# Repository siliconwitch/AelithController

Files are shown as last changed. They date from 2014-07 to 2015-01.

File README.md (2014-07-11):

# Project Aelith Digital Controller
=================================

An embedded control system targeted to RC model cars which feature individual wheel drive. This controller allows for software differentials and power delivery with the aid of various sensors on the vehicle. Currently the system makes use of wheel speed sensors and a 6 axis IMU for real time processing.

Overview Video: http://youtu.be/ET1HEyqEQJQ

The controller communicates to a steering servo and four brushless DC motor controllers. It also listens to a standard RC radio receiver for user input, as well as a serial port for telemetry over wireless modules such as xbee or bluetooth.

It's hoped that this project allows for advanced features such as traction control, under/over steer detection, adaptive power delivery and real-time telemetry.

The system runs on Cortex M4 STM32F4 devices by ST microelectronics. To build this project, you will need the ARM-GCC compiler found here:

https://launchpad.net/gcc-arm-embedded

As well as the STLink driver for uploading to a development board such as the STM32F4Discovery board:

http://www.st.com/web/en/catalog/tools/FM146/CL1984/SC724/SS1677/PF251168

To enable debugging, GDB is required and can be found here:

http://www.emb4fun.de/archive/stlink/index.html

The make.bat file is able to run under Windows to compile, upload and start the debug server. Please ensure that your PATH environment variable are set up in windows for the batch commands to be recognized.

Control System
--------------
The control system for the project is designed in Simulink and can be exported as C code using the embedded coder module. Granted this is the only part of the project that requires a non free software, the exported code however is still in readable C. Useful resource: http://www.mathworks.co.uk/hardware-support/arm-cortex-m-cmsis.html and http://www.mathworks.co.uk/hardware-support/st-discovery-board.html

PCB Info
--------

The hardware used in the project is custom. To see the Schematic, Gerber and Diptrace project files, please see the PCB folder.
Bare boards are available to order at: https://oshpark.com/shared_projects/t9Uw3F4U

CAD Designs
-----------

I'll upload full documentation soon on how to modify a Schumacher Mi5 chassis to support four motors, in the meantime, the CAD files for motor mounts, couplings and suspension mounts can be found in the mechanical folder

Copyright
---------

Copyright (C) 2014 Rajesh Nakarja. All rights reserved
http://www.naklojik.com

This is free software; you can redistribute it and/or modify it under the 
terms of the GNU Lesser General Public License version 3.0.
http://opensource.org/licenses/lgpl-3.0.html

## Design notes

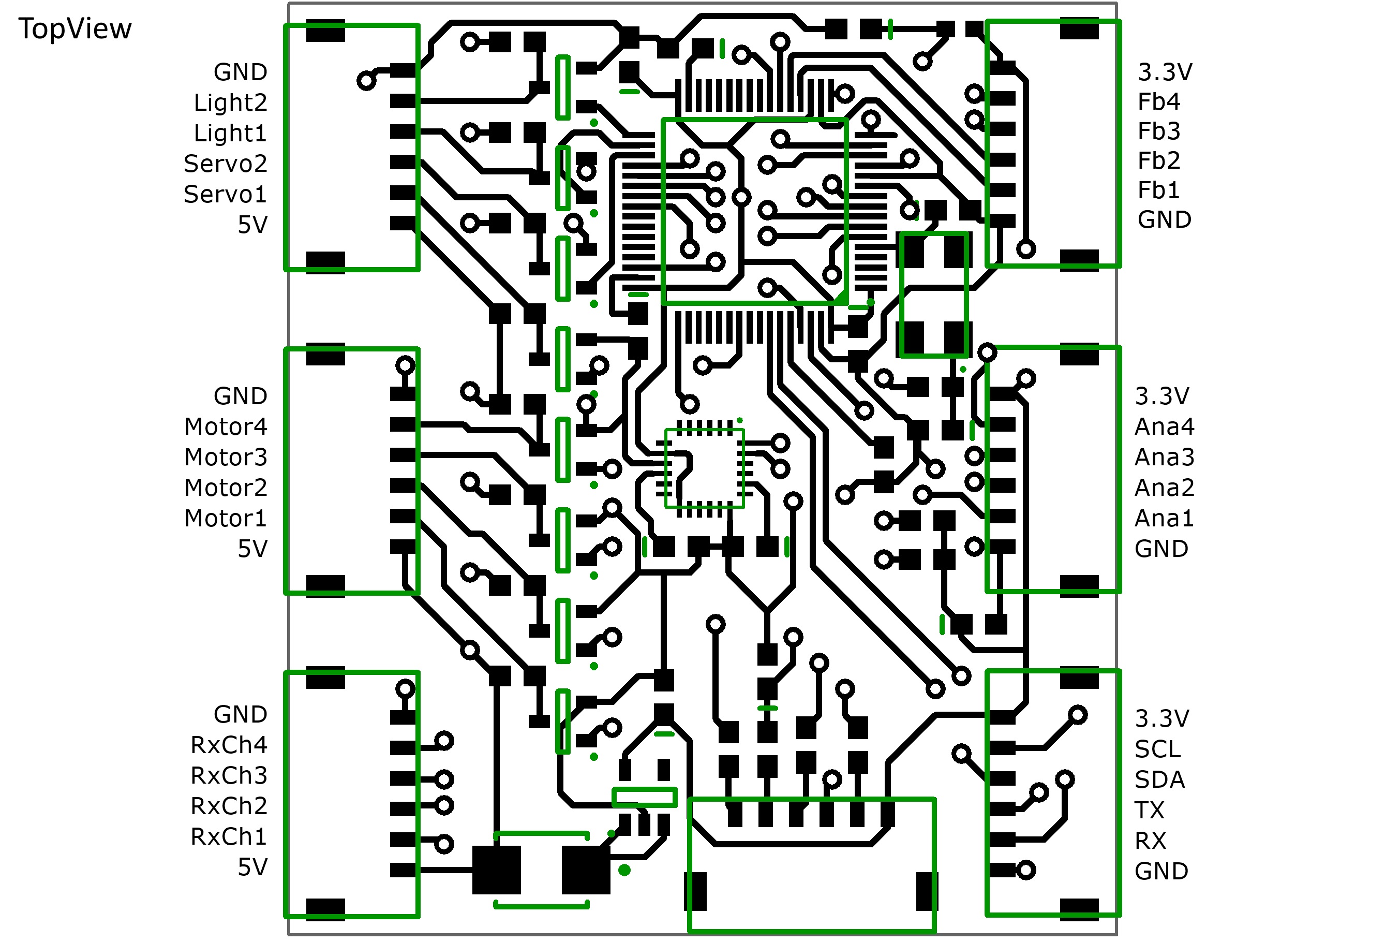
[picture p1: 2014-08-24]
PCB & CAD/PCB Pinout.jpg

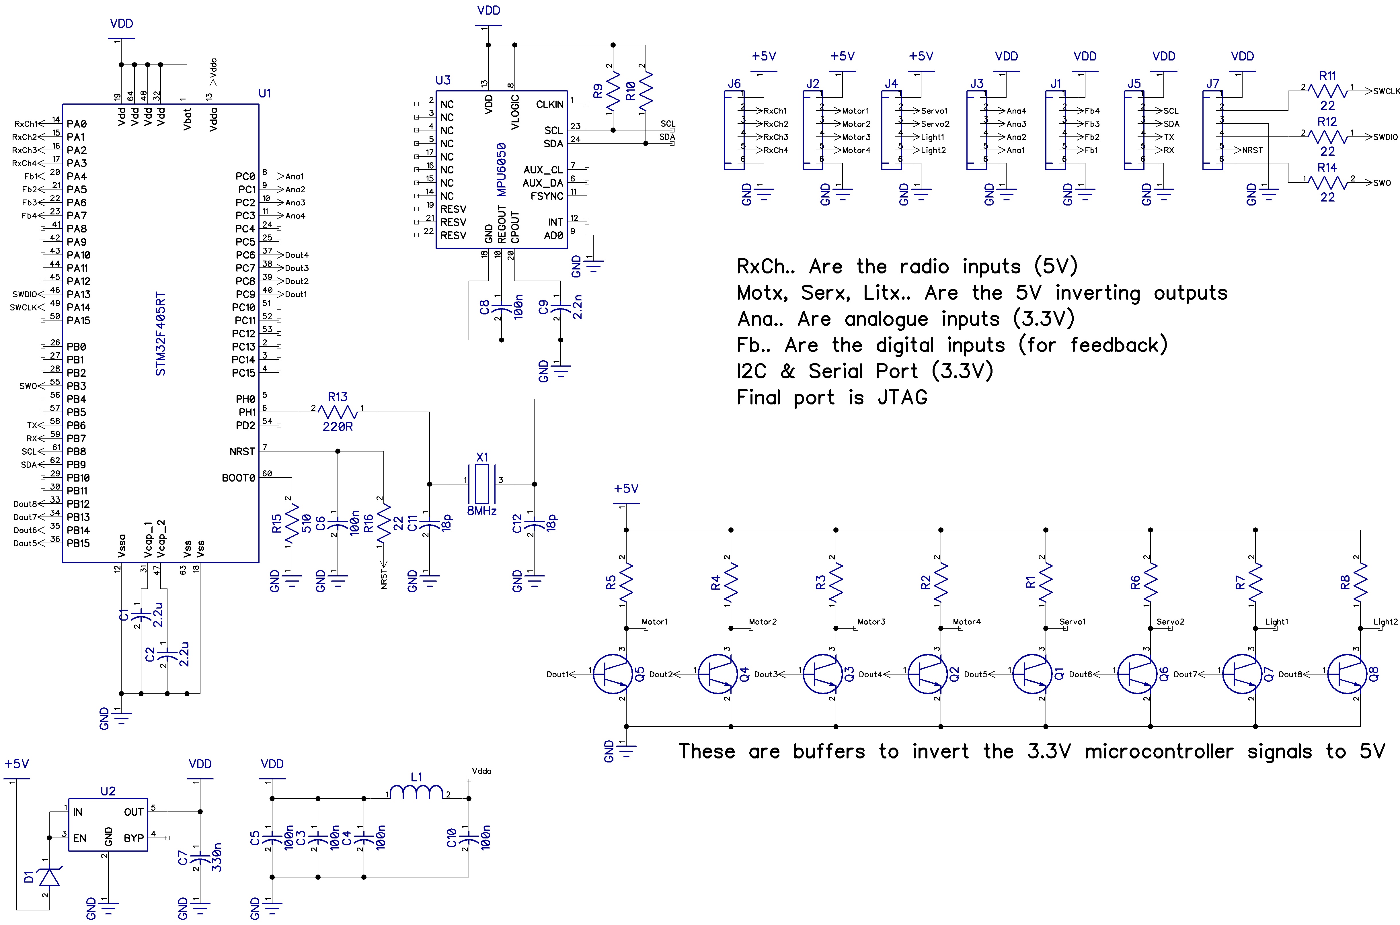
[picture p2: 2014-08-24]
PCB & CAD/Schematic.jpg

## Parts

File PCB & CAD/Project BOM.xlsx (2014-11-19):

Item | Quantity | Single Cost | Total Cost | Link | | | Comments
------------------------------------------------------------------------------------------------------------------------------------------------- |  |  |  |  | | | ---------------------------------------
Schumacher Mi5 | 1 | £344.84 | £344.84 | http://www.wheelspinmodels.co.uk/i/194938/
35A Hobbyking Sensor/Sensorless ESC | 4 | £15.53 | £62.12 | http://www.hobbyking.com/hobbyking/store/__17228__Hobby_King_35A_Sensored_Sensorless_Car_ESC_1_10_1_12_.html
Quadcopter Motors | 4 | £15.89 | £63.56 | http://www.hobbyking.com/hobbyking/store/uh_viewitem.asp?idproduct=41483
Tunigy 4.2 2S2P Shorty Hard Lipo | 1 | £22.14 | £22.14 | http://www.hobbyking.com/hobbyking/store/__23134__Turnigy_nano_tech_Shorty_4200mah_2S2P_65_130C_Hardcase_Lipo_Pack_ROAR_APPROVED_.html
BMS Metal Gear Servo | 1 | £12.63 | £12.63 | http://www.hobbyking.com/hobbyking/store/uh_viewItem.asp?idProduct=43502
4mm Bullet Connectors (3pk) | 4 | £2.57 | £10.28 | http://www.hobbyking.com/hobbyking/store/uh_viewItem.asp?idProduct=40777
AMG SLS GT3 Body | 1 | £32.90 | £32.90 | http://www.ebay.co.uk/itm/121104674654?ssPageName=STRK:MEWNX:IT&_trksid=p3984.m1439.l2649
2.4GHz Turnigy Radio | 1 | £24.86 | £24.86 | http://www.hobbyking.com/hobbyking/store/__23165__Turnigy_GTX3_AFHDS_2_4ghz_3_Channel_Radio_System.html
IMAX B6 Charger | 1 | £16.49 | £16.49 | http://www.hobbyking.com/hobbyking/store/__5548__IMAX_B6_Charger_Discharger_1_6_Cells_GENUINE_.html
3D Printed Parts | 1 | 36.58 | £36.58 | http://i.materialise.com/

 |  | Total | £626.40
Consumable Item | Quantity | Single Cost | Total Cost | Link | | | Comments
------------------------------------------------------------------------------------------------------------------------------------------------- |  |  |  |  | | | ---------------------------------------
Road Wheels | 1 | £9.99 | £9.99 | http://www.ebay.co.uk/itm/211000143-1-10-Scale-On-Road-Wheel-Tyres-Nitro-RC-Car-Black-Soft-Tree-V4-/261073439493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
Drift Wheels | 1 | £11.64 | £11.64 | http://www.ebay.co.uk/itm/1-10-10-SPOKE-WHITE-RC-DRIFT-WHEEL-TYRE-SET-3mm-OS-IDEAL-TAMIYA-TT01-UK-POST-/251297528979

 |  | Total | £21.63

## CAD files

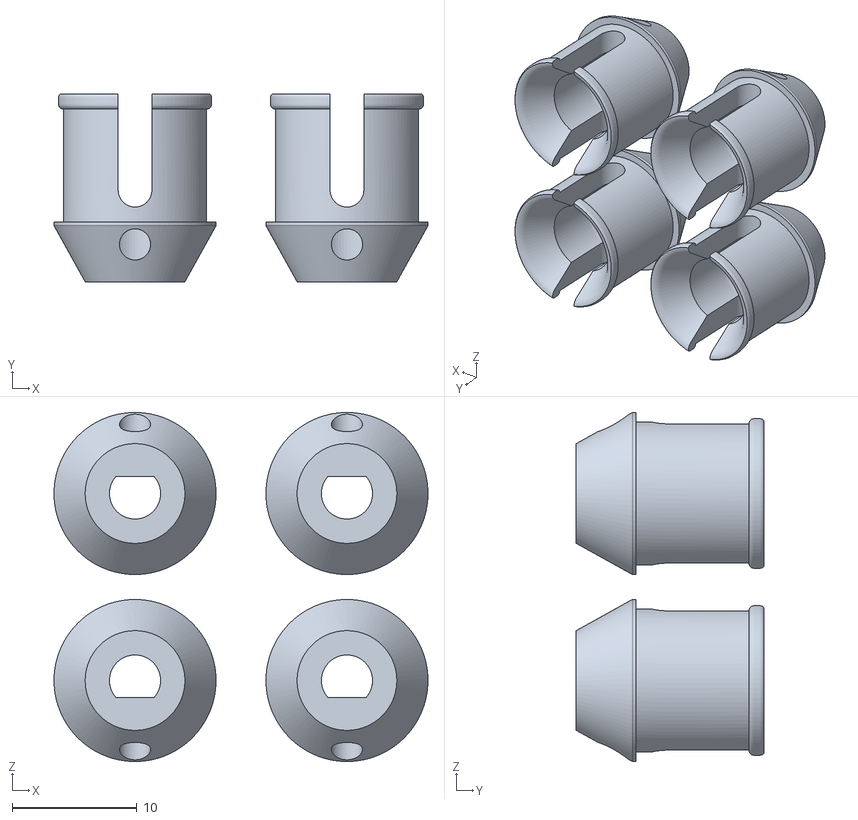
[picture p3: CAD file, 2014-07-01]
PCB & CAD/Couplings-V10.stl
30.0 x 15.1 x 28.0

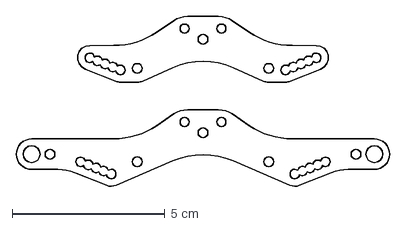
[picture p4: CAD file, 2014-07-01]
PCB & CAD/Suspension Mounts-V13.dxf
12.2 x 5.56 cm

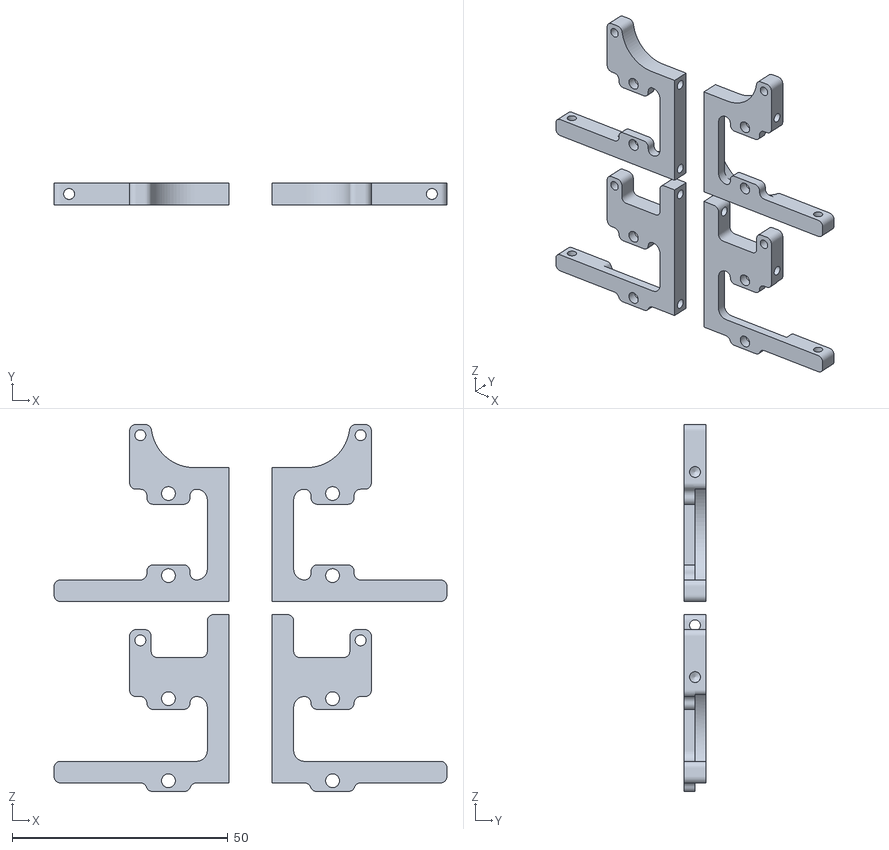
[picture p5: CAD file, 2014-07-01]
PCB & CAD/Rear mounts-V21.stl
91.0 x 5.00 x 85.0

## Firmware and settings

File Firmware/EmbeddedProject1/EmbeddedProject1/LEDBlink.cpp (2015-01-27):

#include <stm32f4xx_hal.h>

#ifdef __cplusplus
extern "C"
#endif
void SysTick_Handler(void)
{
	HAL_IncTick();
	HAL_SYSTICK_IRQHandler();
}

int main(void)
{
	HAL_Init();

	__GPIOD_CLK_ENABLE();
	GPIO_InitTypeDef GPIO_InitStructure;

	GPIO_InitStructure.Pin = GPIO_PIN_12;

	GPIO_InitStructure.Mode = GPIO_MODE_OUTPUT_PP;
	GPIO_InitStructure.Speed = GPIO_SPEED_HIGH;
	GPIO_InitStructure.Pull = GPIO_NOPULL;
	HAL_GPIO_Init(GPIOD, &GPIO_InitStructure);

	for (;;)
	{
		HAL_GPIO_WritePin(GPIOD, GPIO_PIN_12, GPIO_PIN_SET);
		HAL_Delay(500);
		HAL_GPIO_WritePin(GPIOD, GPIO_PIN_12, GPIO_PIN_RESET);
		HAL_Delay(500);
	}
}

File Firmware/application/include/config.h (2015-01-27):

 /*
 * Brief:       Main config, pin mappings and global variables for Project Aelith.
 *
 *				From here we can see all the major variables shared	between the 
 *				vehicle control system as well as all the peripherals. There are
 *				also many config values that can be tweaked for different setups.
 *
 * Copyright (C) 2014 Rajesh Nakarja. All rights reserved
 * http://www.naklojik.com
 *
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
 * http://opensource.org/licenses/lgpl-3.0.html
 *
 */

#ifndef __PINMAPPINGS_H
#define __PINMAPPINGS_H
 
/*------------------------*/
/* INITIAL CONFIGURATION  */
/*------------------------*/
	/* Motor related */
	#define MOTORPOLES	14

	/* ADC related */
	#define ADCSAMPLES	ADC_SAMPLETIME_15CYCLES

	/* Serial related */
	#define BAUDRATE 	9600

	/* Receiver related */
 	#define PPMTIMEOUTVALUE		50000
 	#define PPMTIMEOUTPRESCALER	42

 	#define PPMMEASUREPRESCALER	4
 	#define RECEIVERMINSIGNAL	16000
 	#define RECEIVERMIDSIGNAL	25000
 	#define RECEIVERMAXSIGNAL	34000

	/* IMU related */
	#define DEFAULTACCELRANGE	4
	#define DEFAULTGYRORANGE	500
 	#define TIMEOUT 			1000

	/* Control related */
	#define POWERBIAS 0
	#define FRONTSLIP 0.95
	#define REARSLIP 0.1
 	#define GYROGAIN 0.0 //0.9

/*------------------------*/
/* PIN MAPPINGS FOR BOARD */
/*------------------------*/
	/* This is just a reference, don't change these pins without 
	   checking where they are used. Each pin also have
	   interrupts tied to them, so they'd also need changing */

	/* Pins and port for motor outputs */
	#define MOTOR1PIN	GPIO_PIN_6		/* FL Wheel */
	#define MOTOR2PIN	GPIO_PIN_7		/* FR Wheel */
	#define MOTOR3PIN	GPIO_PIN_8		/* BL Wheel */
	#define MOTOR4PIN	GPIO_PIN_9		/* BR Wheel */
	#define MOTORPORT	GPIOC

	/* Pins and port for AUX outputs */
	#define AUX1PIN		GPIO_PIN_12
	#define AUX2PIN		GPIO_PIN_13
	#define AUX3PIN		GPIO_PIN_14
	#define AUX4PIN		GPIO_PIN_15
	#define AUXPORT		GPIOB

	/* Serial port pins */
	#define TXPIN		GPIO_PIN_6
	#define RXPIN		GPIO_PIN_7
	#define SCLPIN		GPIO_PIN_8
	#define SDAPIN		GPIO_PIN_9
	#define DATAPORT	GPIOB

	/* Hallsensor feedback input pins */
	#define FB1PIN		GPIO_PIN_4
	#define FB2PIN		GPIO_PIN_5
	#define FB3PIN		GPIO_PIN_6
	#define FB4PIN		GPIO_PIN_7
	#define FBPORT		GPIOA

	/* Receiver input channel pins */
	#define REC1PIN		GPIO_PIN_0
	#define REC2PIN		GPIO_PIN_1
	#define REC3PIN		GPIO_PIN_2
	#define REC4PIN		GPIO_PIN_3
	#define RECPORT		GPIOA

	/* Analogue input pins */
	#define ANA1PIN		GPIO_PIN_0
	#define ANA2PIN		GPIO_PIN_1
	#define ANA3PIN		GPIO_PIN_2
	#define ANA4PIN		GPIO_PIN_3
	#define ANAPORT		GPIOC

/*------------------------*/
/*    GLOBAL VARIABLES    */
/*------------------------*/

	typedef struct { double steering, throttle, aux1, aux2; } RCRadio;

	typedef struct { double MOT1, MOT2, MOT3, MOT4, AUX1, AUX2, AUX3, AUX4; } PPMOutputs;

	typedef struct { double FL, FR, BL, BR; } WheelRPM;

	typedef struct { uint16_t ch1,  ch2,  ch3,  ch4; } AnalogueOutput; //currently unused

	typedef struct { float x, y, z, roll, pitch, yaw, temp, valid; } IMUMotion;

	uint8_t telemetryFlag;

#endif

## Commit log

2014-06-06 Major updates
    Fixed pin clash on I2C and serial, Fixed IMU settings, read and
    conversions, rewrote file description comments, added LGPLv3 licence to
    all files
    [analogue.c, imu.c, serial.c]
2014-06-07 Merged hallsensors and rcradio
    Both these files shared resources so they were merged. Also the external
    interrupts where rearranged and input pins finalised for PCB
2014-06-08 Finished IO assignments, tested and working
    Timers also rearranged
2014-06-30 Updated device
    Updated make.bat to support new device: STM32F405RG
2014-07-01 Outputs & watchdog working. Massive cleanup
    PPM Outputs work, Watchdog added, Config file added, merged all header
    files for better organisation (prototypes.h)
2014-07-01 Added PCB and CAD files
    [Couplings v9.stl, Motor Mounts v19.stl, Suspension Mounts v13.dxf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]
2014-07-01 Updated Readme, Added CAD files
    Added the PCB and mechanical hardware CAD files to the project
    [Couplings v9.stl, Couplings-V10.stl, Motor Mounts v19.stl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]
2014-07-03 Fixed receiver input & fail safes
    Lost receiver signal and invalid signal are now fixed
    [config.h, serial.c]
2014-07-03 I2C burst read, ADC DMA interrupt
    Added features, IMU is read with a burst and ADC result is put in a
    structure using a DMA interrupt handler
2014-07-04 Normalised PPM input and output
    The signal into and out of the platform is now normalised from (double)
    -1 to 1. We can now use these to apply algorithms to.
    normalisedSignal(uint32_t input) converts from timer to double and
    denormaliseSignal(double input) converts double to uint32_t
2014-07-06 First control!
    First control algorithm working, fixed slightly short receiver timer
    value which was causing problems.
    Made failsafes more integrated. RCRadioStructure no longer holds the
    failsafe flags, they structure is only given valid steering/throttle/aux
    values if valid radio signal, otherwise its zeroed. Removed labview code
    generation. It's too messy to implement. We're better off writing our
    own algorithms efficeint derived from the labview models
    [config.h]
2014-07-07 Moved to Simulink. Wheel sensors fixed
    Simulink code generation has worked. Wheel speed sensing is fixed. Was
    mostly a sensor placement issue on the car. Wheel speed timeout code is
    fixed.
    [config.h]
2014-07-11 Added BMP of Schematic and PCB Pinout
2014-07-17 Moved to new HAL drivers for stm32
2014-07-27 Updated control system & serial link
    Corrective steering works, serial working (unstable), started work on
    wheel speed feedback
    [analogue.c, config.h, imu.c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]
2014-08-24 Converted Schematics to JPEG
    The bitmap files were huge
2014-11-19 Changed PCB folder structure
    [Project BOM.xlsx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]
